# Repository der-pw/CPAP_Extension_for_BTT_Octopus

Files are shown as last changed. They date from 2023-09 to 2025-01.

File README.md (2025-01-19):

# CPAP Extension for BTT Octopus
... and some other boards  

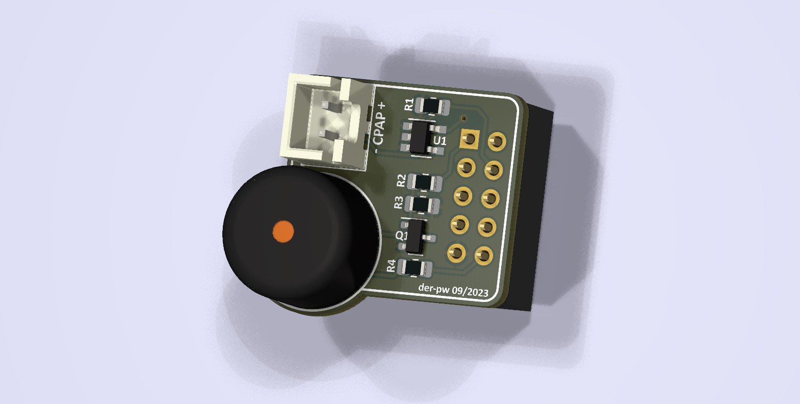
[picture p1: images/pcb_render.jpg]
render image of the PCB


## Extension to add the CPAP function without giving up the Neopixel port.
The WS7040 “CPAP Cooling Controller” requires a positive 5V switching signal to control the speed of the motor. For some boards like the BTT Octopus, the workaround is to use the pin for Neopixel (PB0 or PB10).
But if you don't want to loose out the fancy Neopixel Blinky thing, you can attach this little board to the EXP1 port. In most cases we don't need EXP1 because we have a display connected to the SBC (Raspberry Pi, etc.).

### Pin mapping
I choosed the ports for **BEEPER** and **LCD_RS**.
On the Octopus Pro V1.1 this corresponds to pins `PE8` and `PE10`.
According to the data sheet of the used STM, they can PWM, and that's exactly what we need.

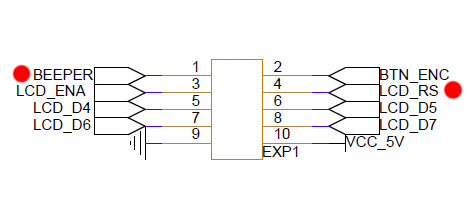
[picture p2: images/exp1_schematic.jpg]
schematic of EXP1
  

The beeper is additional. Some extra informations via speaker are helpful. :smile:  

Information about the pin mapping on other boards.  
Do you miss one here? Please let me know!  

| Board (Version)  | Description | Mapping new | PIN
| --- | --- | --- | :---: |
| BTT Octopus Pro V1.1 | *STM32H723ZET6*| | |
| | BEEPER | BUZZER | `PE8`  |
| | LCD_RS | CPAP Control| `PE10`  |
| BTT Octopus V1.0 | *STM32F446ZET6*| | |
| | BEEPER | BUZZER | `PE8` |
| | LCD_RS | CPAP Control| `PE10`  |
| Fysetc Cheetah V3.0 (EXP3) | *STM32F446RCT6* | | |
| | BEEP | BUZZER | `PB10` |
| | LCD_RS | CPAP Control| `PB14`  |

### Parts
| Position | Description | Value | Information
| --- | --- | --- | ---
| R1 | Resistor | 4.7k | SMD 0805
| U1 | Buffer Gate | 74LVC1G125 | https://www.ti.com/lit/ds/symlink/sn74lvc1g125.pdf
| J1 | IDC Connector for EXP1 | SFH11-PBPC-D05-ST-BK | https://www.digikey.com/de/products/detail/sullins-connector-solutions/SFH11-PBPC-D05-ST-BK/1990087
| J2 | JST XH male | pitch 2.54 | https://de.aliexpress.com/item/1005003422202370.html
| optional | | |just if you want the buzzer
| R2 | Resistor | 330 | SMD 0805
| R3 | Resistor | 4.7K / 10k | SMD 0805
| Q1 | N-MOSFET | AO4300A | SOT-23
| BZ1 | Buzzer (passive) | 12x8.5mm  6.6mm Pitch | https://www.amazon.de/dp/B0179I6LIK 

All SMD parts are specified in the production file. I have no experience with assembling THT parts via the SMT service, so I always solder them by hand. In this case this applies to the buzzer, the JST connector and the IDC connector.

U1 buffer gate is the same level shifter as the one in the Octopus Board. The IDC Connector J1 is hard to find. Sometimes it's available at aliexpress, or you have a friendly Guy, he can order at digikey.
A 2x5 (2.54mm) pin header will also work, but please be aware to check the direction if you put it in your board.

### Place the addon into your board
Here you can see where the addon is located on the BTT Octopus Pro.  

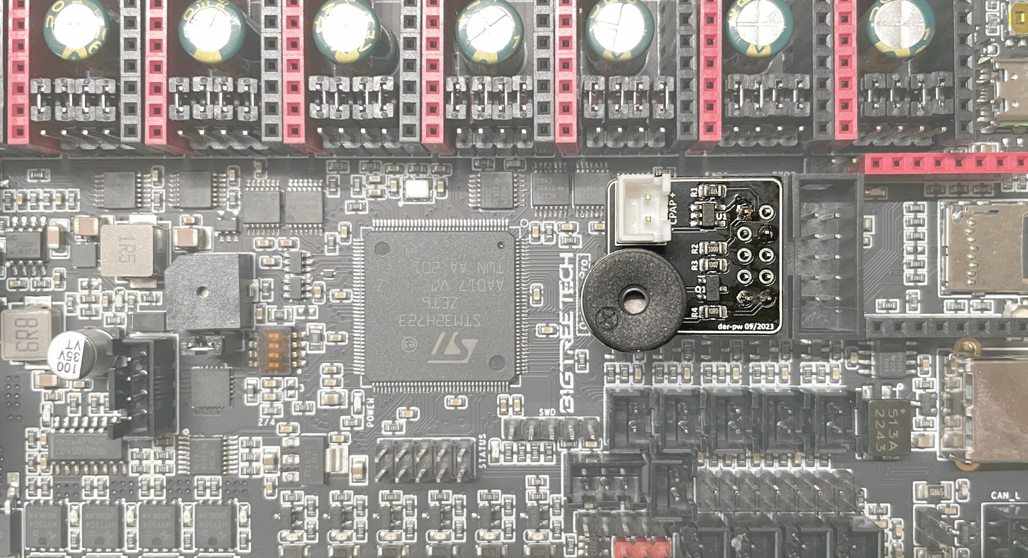
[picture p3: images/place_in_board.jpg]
place in board


### Connection to controller board
Connect the + pin from the expansion board to the VSR pin from the controller (Pin 2).
In addition, the - pin with the GND pin (Pin 3), even if it is not absolutely necessary.

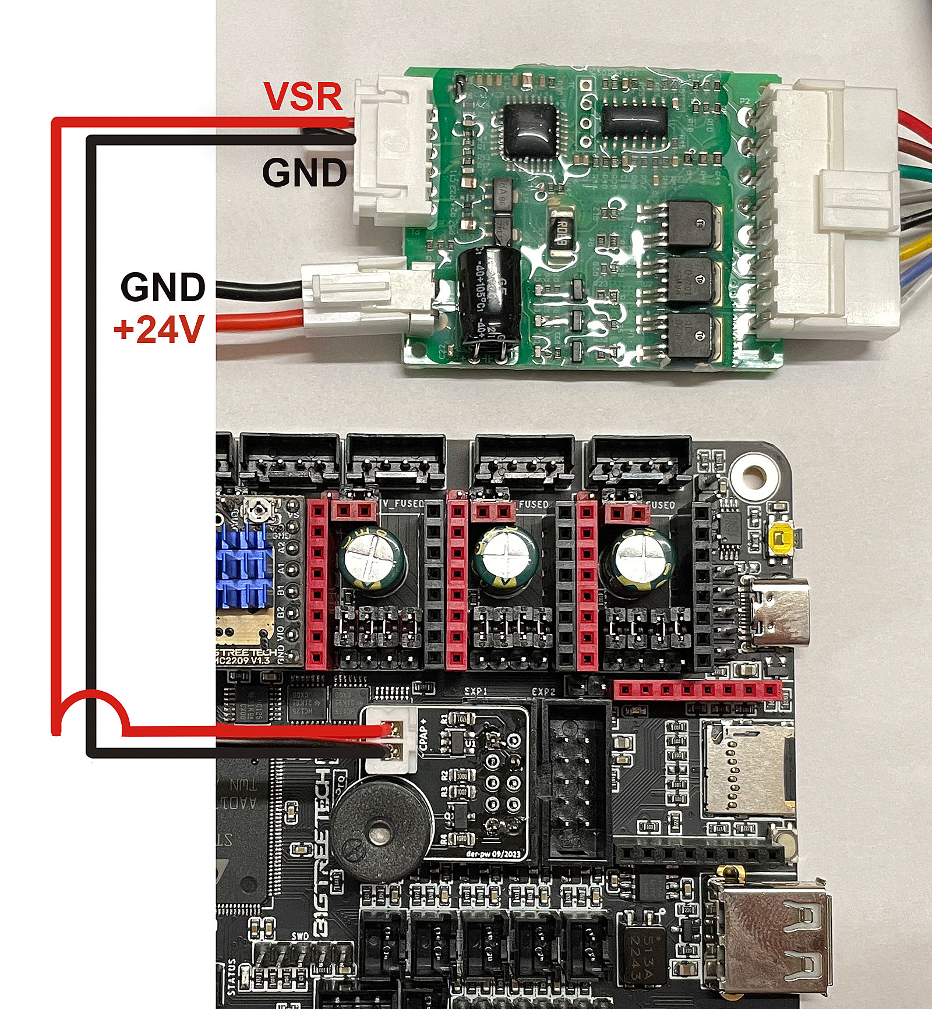
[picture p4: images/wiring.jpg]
wiring


### Klipper config
I've set the cycle time to 0.00004 (25 kHz.) This is how I got the best results and can set the power down to 6%.

```
[fan]
pin: PE10
max_power: 1.0
kick_start_time: 0.1
cycle_time: 0.00004 #25kHz
hardware_pwm: False
off_below: 0.06
```

### Additional buzzer function
Please check the configuration file in *klipper* folder.
You can copy the *macro_buzzer.cfg* into your configuration folder and include it in your *printer.cfg* with `[include macro_buzzer.cfg]`.
Enable the correct pin depending on your board.
Now you will get some tones about `M300`.
For example, you can use `M300 S440 P1000` to play a tone at 440 Hz for 1 second. In *macro_buzzer.cfg* you'll find some macros that play small melodies.

### Resistor for the buzzer
I have added a resistor in series to the buzzer with 10Ω to reduce resonances in some fequencies. If you need it louder or quieter, you can chance R4 with other values.

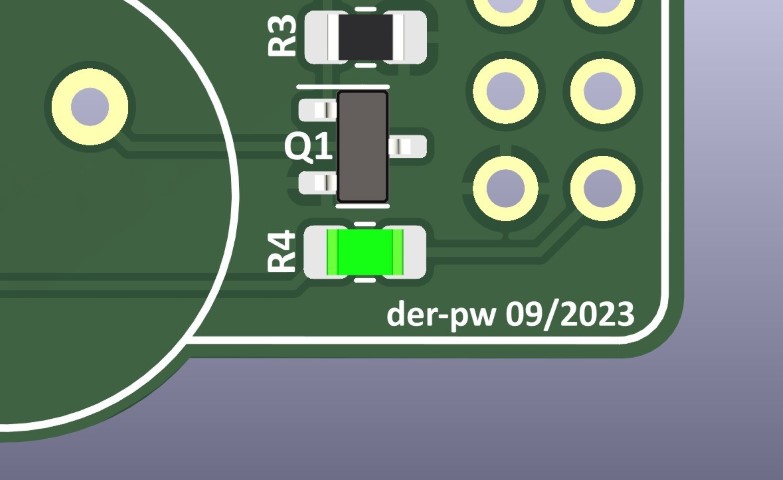
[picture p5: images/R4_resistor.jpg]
R4 Resistor


### FAQ
*Why not to connect to one of the many FAN ports?*  
The fan ports are controlled by a N-channel MOSFET. You just can controll the negative side with PWM but you need the positive side, because the VSR input has common GND.

*Why not to connect to the GPIO of my Raspberry Pi?*  
It's the same like at some pins of your Octopus Board. They just have a logic level of 3.3V. The VSR Input of the CPAP controller needs 5V for 100% cooling power. You lose around 30%.

*Does this also work with other boards?*  
So far I have only tested it with the Octopus, Octopus Pro and the Fysetc Cheetah 3.0. It should work with many boards that offer a slot for a 12864 display. However, you then have to check whether a pin with a PWM signal arrives at the positions I used.

--- 

### This is Open Source Hardware

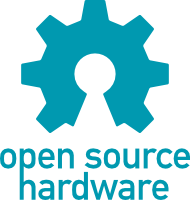
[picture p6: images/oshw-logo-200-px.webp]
open source hardware
  
Feel free to create your own modifiactions and versions!

Gerbers are made with [Fabrication Toolkit](https://github.com/bennymeg/JLC-Plugin-for-KiCad).

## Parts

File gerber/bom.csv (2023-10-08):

Designator | Footprint | Quantity | Value | LCSC Part #
Q1 | SOT-23 | 1 | AO3400A | C20917
R1 | 0805 | 1 | 4.7k | C17673
R2 | 0805 | 1 | 300R | C17617
R3 | 0805 | 1 | 10k | C17414
R4 | 0805 | 1 | 10R | C17415
U1 | SOT-23-5_HandSoldering | 1 | 74LVC1G125 | C23654

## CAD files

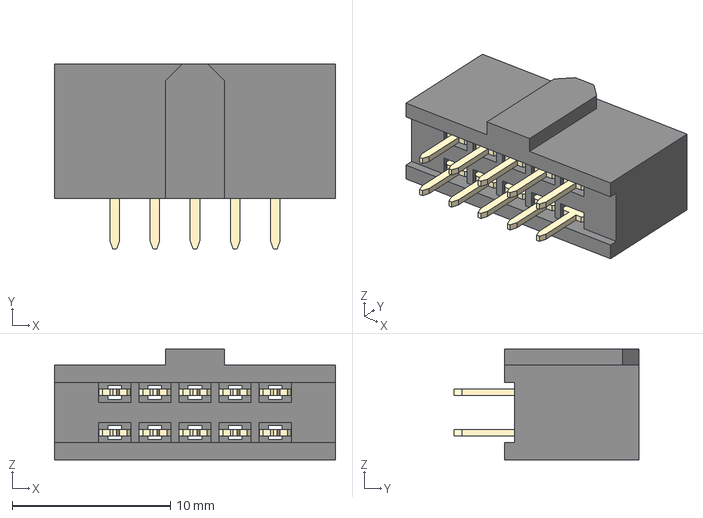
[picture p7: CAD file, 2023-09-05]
kicad7.0/SFH11-PBPC-D05-ST-BK--3DModel-STEP-56544.STEP
17.8 x 11.7 x 7.01 mm
SFH11-xC-Dx-ST-BK body_05
pin^SFH11-xC-Dx-ST-BK Ass x 10

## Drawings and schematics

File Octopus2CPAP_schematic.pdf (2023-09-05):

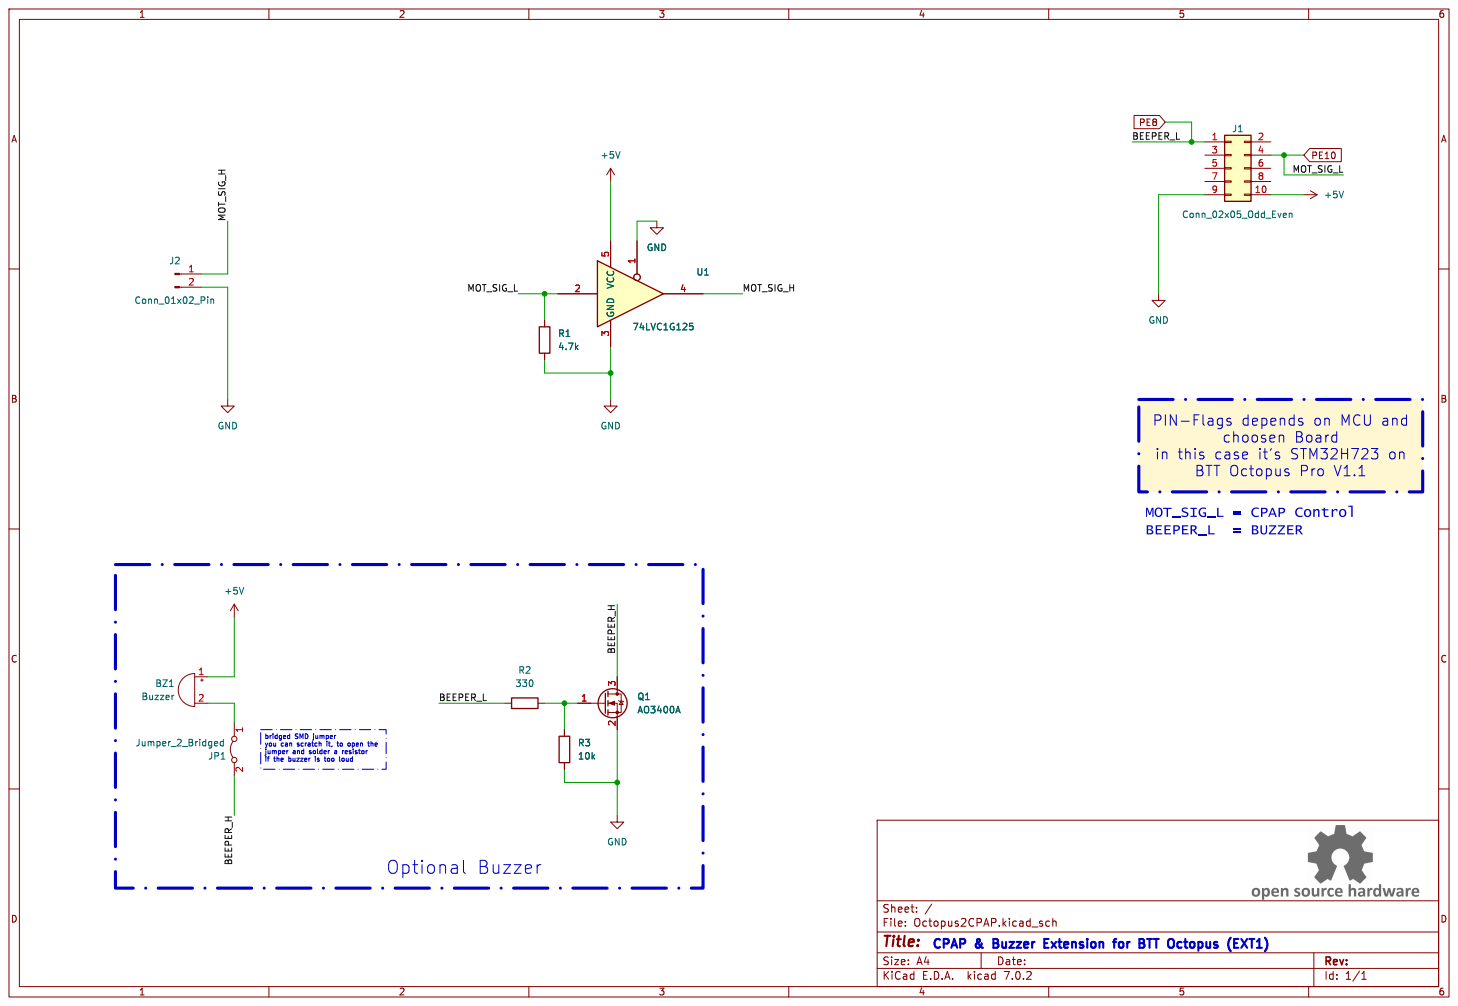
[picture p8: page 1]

in this case it's STM32H723 on BTT Octopus Pro V1.1

Id: 1/1 Title: File: Octopus2CPAP.kicad_sch Sheet: / 1 2

jumper and solder a resistor

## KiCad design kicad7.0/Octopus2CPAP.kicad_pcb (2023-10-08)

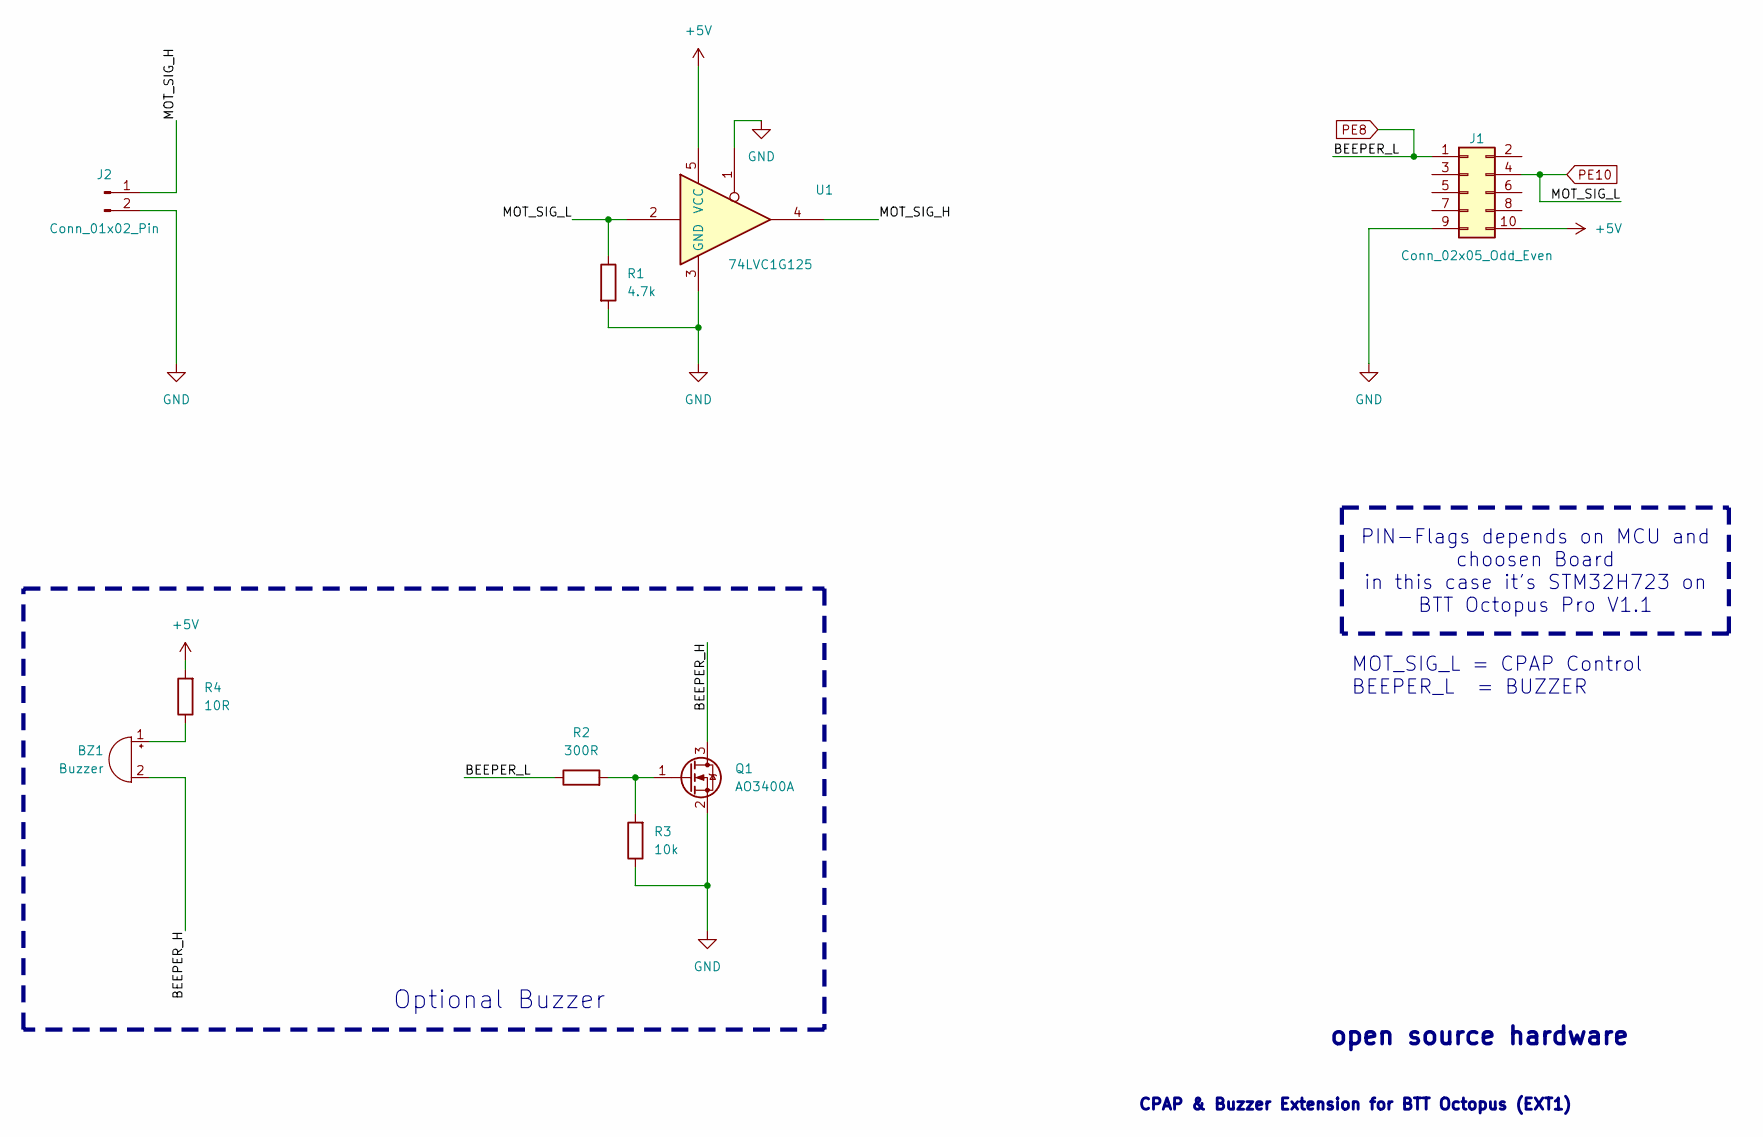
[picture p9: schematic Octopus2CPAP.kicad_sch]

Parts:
BZ1: Buzzer; Buzzer_12x9.5RM7.6
J1: Conn_02x05_Odd_Even; PinSocket_2x05_P2.54mm_Vertical
J2: Conn_01x02_Pin; JST_XH_B2B-XH-A_1x02_P2.50mm_Vertical
Q1: AO3400A; SOT-23; MPN C20917; JLCPCB Rotation Offset 180
R1: 4.7k; R_0805_2012Metric_Pad1.20x1.40mm_HandSolder; MPN C17673
R2: 300R; R_0805_2012Metric_Pad1.20x1.40mm_HandSolder; MPN C17617
R3: 10k; R_0805_2012Metric_Pad1.20x1.40mm_HandSolder; MPN C17414
R4: 10R; R_0805_2012Metric_Pad1.20x1.40mm_HandSolder; MPN C17415
U1: 74LVC1G125; SOT-23-5_HandSoldering; MPN C23654; JLCPCB Rotation Offset -90

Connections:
+5V: J1.10, R4.2, U1.5 (VCC)
/BEEPER_H: BZ1.2 (+), Q1.3 (D)
/MOT_SIG_H: J2.1, U1.4
GND: J1.9, J2.2, Q1.2 (S), R1.2, R3.1, U1.1, U1.3 (GND)
unnamed: BZ1.1 (-), R4.1
unnamed: Q1.1 (G), R2.2, R3.2
PE8: J1.1, R2.1
PE10: J1.4, R1.1, U1.2

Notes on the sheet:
PIN-Flags depends on MCU and choosen Board in this case it's STM32H723 on BTT Octopus Pro V1.1
MOT_SIG_L = CPAP Control BEEPER_L = BUZZER
open source hardware
Optional Buzzer
CPAP & Buzzer Extension for BTT Octopus (EXT1)

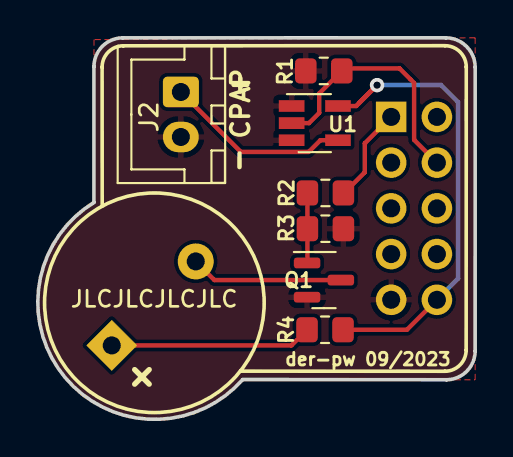
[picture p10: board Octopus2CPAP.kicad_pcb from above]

Board: 2 copper layers, 24.3 x 21.2 mm, 9 parts (1 on the bottom side), 8 nets.

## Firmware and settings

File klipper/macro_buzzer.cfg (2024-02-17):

#########################################
##### add this to your printer.cfg ######
## best via [include macro_buzzer.cfg] ##
#########################################

[pwm_cycle_time _BEEPER_pin]
#pin: PE8  # check if it's the right pin for your board https://github.com/der-pw/CPAP_Extension_for_BTT_Octopus#pin-mapping
shutdown_value: 0
cycle_time: 0.1
scale: 1


[gcode_macro M300]
gcode:
    # Use a default 1kHz tone if S is omitted.
    {% set S = params.S|default(1000)|int %}
    # Use a 100ms duration is P is omitted. (100ms is the fastest switching limit)
    {% set P = params.P|default(100)|int %}
    {% if S > 0 %}
    SET_PIN PIN=_BEEPER_pin VALUE=0.1 CYCLE_TIME={ 1.0/S if S > 0 else 1 }
    {% endif %}
    G4 P{P}
    SET_PIN PIN=_BEEPER_pin VALUE=0


##########################
## start and stop print ##
##########################

[gcode_macro _PLAY_START_PRINT]
gcode:
    M300 S1319 P50
    M300 S1568 P50
    M300 S2093 P500

[gcode_macro _PLAY_STOP_PRINT]
gcode:
    M300 S2093 P50
    M300 S1568 P50
    M300 S1319 P500


##########################
##  some funny things   ##
##########################

[gcode_macro _PLAY_SUPERMARIO_ONE_UP]
description: Plays the "1 UP!" tune from Super Mario Bros
gcode:
    M300 S1319 P125
    M300 S1568 P125
    M300 S2637 P125
    M300 S2093 P125
    M300 S2637 P125
    M300 S3136 P125

[gcode_macro _PLAY_ENTERTAINER]
description: Plays a part of the entertainer tune
gcode:
    M300 P211 S294
    M300 P211 S311
    M300 P211 S330
    M300 P211 S523
    M300 P211 S262
    M300 P211 S330
    M300 P423 S523
    M300 P211 S330
    M300 P211 S523
    M300 P423 S175
    M300 P423 S262
    M300 P211 S165
    M300 P211 S1047
    M300 P211 S1175
    M300 P211 S1245
    M300 P211 S1319
    M300 P211 S1047
    M300 P211 S1175
    M300 P211 S1319
    M300 P211 S98
    M300 P211 S988
    M300 P423 S1175
    M300 P423 S1047
    M300 P423 S262
    M300 P423 S262

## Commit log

2023-09-04 initial upload
    [Octopus2CPAP.kicad_pcb, Octopus2CPAP.kicad_sch, Octopus2CPAP.step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]
2023-09-05 some changes at pcb
    [Octopus2CPAP.kicad_pcb, Octopus2CPAP.kicad_sch, Octopus2CPAP.step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]
2023-09-05 update gerber
    [bom.csv, designators.csv, positions.csv]
2023-09-30 finalize board
2023-10-08 finalize and release
    [Octopus2CPAP.kicad_pcb, Octopus2CPAP.kicad_sch, Octopus2CPAP.step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]
2024-02-17 Update macro_buzzer.cfg
    change output_pin to pwm_cycle_pin
    [macro_buzzer.cfg]
2025-01-19 Update README.md
    added pin location
